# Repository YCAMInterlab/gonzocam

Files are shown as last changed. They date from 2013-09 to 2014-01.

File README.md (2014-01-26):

# gonzocam


Open source hardware kit for disposable camera or iPhone to take pictures of wild animals automatically.

gonzocam（ゴンゾカム）は市販のインスタントカメラを使って人間含む野生動物を自動撮影するためのオープンソースハードウェアキットです。インスタントカメラに装着することで、周囲の物体の動きや加速度の変化などをトリガーにシャッターを切り、自動的にフィルムを巻き上げるなどカメラ本来の機能を拡張することができます。

詳しい情報は[YCAM Interlab | gonzocam](http://interlab.ycam.jp/projects/gonzocam)を参照してください。

## Licenses

### Hardware of gonzocam

<a rel="license" href="http://creativecommons.org/licenses/by-sa/3.0/deed.en_US">
</a>
<br />
<span xmlns:dct="http://purl.org/dc/terms/" property="dct:title">Circuit diagram, Parts list, Gerber format data</span> by <a xmlns:cc="http://creativecommons.org/ns#" href="http://yang02.org/" property="cc:attributionName" rel="cc:attributionURL">yang02</a> is licensed under a <a rel="license" href="http://creativecommons.org/licenses/by-sa/3.0/deed.en_US">Creative Commons Attribution-ShareAlike 3.0 Unported License</a>.

### Software of gonzocam

Arduino sketch by Takahiro Yamaguchi is licensed under the [Apache License, Version2.0](http://www.apache.org/licenses/LICENSE-2.0.html)

    Copyright 2013 Takahiro Yamaguchi

    Licensed under the Apache License, Version 2.0 (the "License");
    you may not use this file except in compliance with the License.
    You may obtain a copy of the License at

       http://www.apache.org/licenses/LICENSE-2.0

    Unless required by applicable law or agreed to in writing, software
    distributed under the License is distributed on an "AS IS" BASIS,
    WITHOUT WARRANTIES OR CONDITIONS OF ANY KIND, either express or implied.
    See the License for the specific language governing permissions and
    limitations under the License.

### Hardware of igonzocam

<a rel="license" href="http://creativecommons.org/licenses/by-sa/3.0/deed.en_US">
</a>
<br />
<span xmlns:dct="http://purl.org/dc/terms/" property="dct:title">Circuit diagram, Parts list</span> by <a xmlns:cc="http://creativecommons.org/ns#" href="http://www.inafact.net/" property="cc:attributionName" rel="cc:attributionURL">inafact</a> is licensed under a <a rel="license" href="http://creativecommons.org/licenses/by-sa/3.0/deed.en_US">Creative Commons Attribution-ShareAlike 3.0 Unported License</a>.

### Software of igonzocam

iOS software by YCAM InterLab and Takanobu Inafuku are licensed under the [Apache License, Version2.0](http://www.apache.org/licenses/LICENSE-2.0.html)

    Copyright 2013 YCAM InterLab and Takanobu Inafuku

    Licensed under the Apache License, Version 2.0 (the "License");
    you may not use this file except in compliance with the License.
    You may obtain a copy of the License at

       http://www.apache.org/licenses/LICENSE-2.0

    Unless required by applicable law or agreed to in writing, software
    distributed under the License is distributed on an "AS IS" BASIS,
    WITHOUT WARRANTIES OR CONDITIONS OF ANY KIND, either express or implied.
    See the License for the specific language governing permissions and
    limitations under the License.

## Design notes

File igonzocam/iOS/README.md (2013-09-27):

# GonzoCam for iOS

## Description

Application for iOS to take pictures of wild animals automatically.

## Requirements & Tested

* Apple Mac OSX 10.8.4+
* Xcode 4.6 + iOS6 SDK (now developing with Xcode 5 + iOS7 SDK)
* [Cinder](http://libcinder.org)
   use latest version from github http://github.com/cinder/Cinder OR [packaged version 0.8.5](http://libcinder.org/download/)
* Tested devices: iPhone 5, iPod Touch(5th Gen)

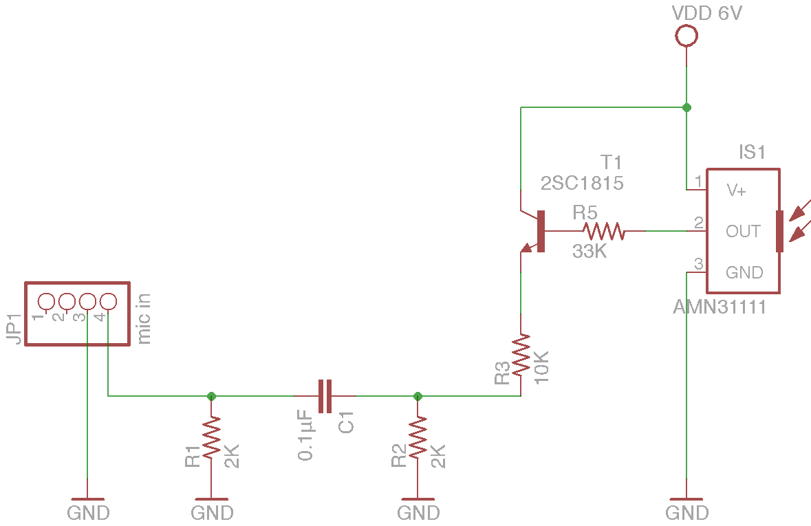
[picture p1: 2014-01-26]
igonzocam/hardware/igonzocam_motionsensor_schematic.png

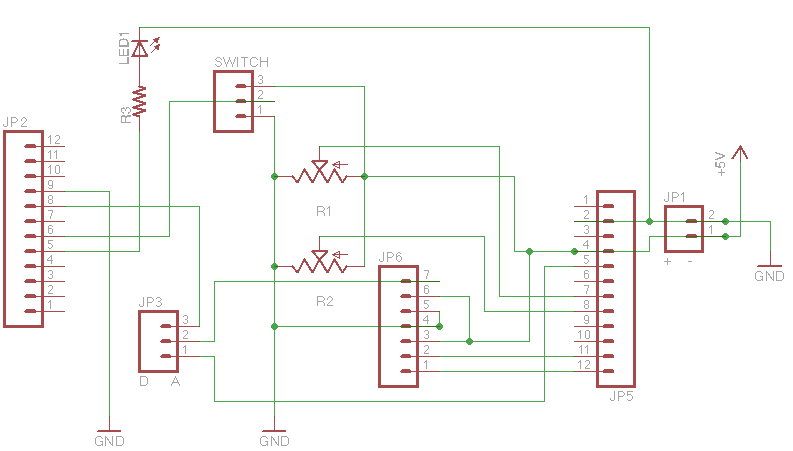
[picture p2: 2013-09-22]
gonzocam/arduino_pro_mini_shield/schematic.png

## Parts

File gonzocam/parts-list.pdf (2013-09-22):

品目 | 単価（円） | 購入先 | URL | 備考
制御基板関係パーツ
Arduino pro mini | 1,094 | スイッチサイエンス | http://www.switch-science.com/catalog/946/
半固定ボリューム | 200 | 秋月 | http://akizukidenshi.com/catalog/g/gP-02470/ | 1パック10個入り
小型スライドスイッチ | 100 | 秋月 | http://akizukidenshi.com/catalog/g/gP-02736/ | 1パック4個入り
カーボン抵抗 1/6W 330Ω | 100 | 秋月 | http://akizukidenshi.com/catalog/g/gR-16331/ | 1パック100本入り
青色LED 3mm | 100 | 秋月 | http://akizukidenshi.com/catalog/g/gI-03988/ | 1パック10個入り
ピンソケット 低メス | 60 | 秋月 | http://akizukidenshi.com/catalog/g/gC-03138/ | 1本20P、Arduino1個につき24P
ピンヘッダ 低オス | 40 | 秋月 | http://akizukidenshi.com/catalog/g/gC-02900/ | 1本40P、1基板につき24P
L字ピンヘッダ | 84 | 千石 | http://www.sengoku.co.jp/mod/sgk_cart/detail.php?code=65KM-8MJG | 1本40P、1基板につき9P
L字ピンヘッダ | 50 | 秋月 | http://akizukidenshi.com/catalog/g/gC-01627/ | 1本40P、上のやつと折れ方が違う
ジャンパーピン | 100 | 秋月 | http://akizukidenshi.com/catalog/g/gP-03687/ | 25個入り
ピンヘッダ オス | 40 | 秋月 | http://akizukidenshi.com/catalog/g/gC-00167/ | 1本40P、1基板につき3P

センサー基板関係パーツ
NaPiOn スポット検出タイプ | 1,103 | 千石 | http://www.sengoku.co.jp/mod/sgk_cart/detail.php?code=5A2C-NNGD
ユニバーサル基板 | 120 | 秋月 | http://akizukidenshi.com/catalog/g/gP-03230/ | Arduino pro miniシールドプリント基板が ない場合は、そこ用にも使用
カーボン抵抗 1/6W 1MΩ | 100 | 秋月 | http://akizukidenshi.com/catalog/g/gR-16105/ | 1パック100本入り
積層セラミックコンデンサ 0.1μF | 100 | 秋月 | http://akizukidenshi.com/catalog/g/gP-06165/ | 25本入り
ロングピンソケット | 70 | 秋月 | http://akizukidenshi.com/catalog/g/gC-05779/ | カメラ1個につき9P
熱収縮チューブ | 50 | 秋月 | http://akizukidenshi.com/catalog/g/gP-06788/

その他の電子パーツ
サーボモータTurnigy TG9e 9g x2 個 | 200 | Hobby King | http://goo.gl/oYUSO | Hobby Kingが一番安いけど届くの超絶遅 いので国内のネット通販で扱ってる店探 すのが吉
電池ボックス 単4x4本 | 150 | 秋月 | http://akizukidenshi.com/catalog/g/gP-00735/
単4電池 | 100 | 100円ショップ | | 1パック4本入り

カメラ＋筐体素材
写ルンです | | コンビニ
アクリル板 3mm | | ホームセンター | 筐体とサーボカバー、一部サーボパーツ 用
アクリル板 5mm | | ホームセンター | サーボヘッド用
さら小ねじ 3Mx20mm | 100 | ホームセンター | 1パック8本入り

その他拡張パーツ等
音声センサーモジュール | 600 | aitendo | http://www.aitendo.com/product/3186
傾きセンサーモジュール | 750 | aitendo | http://www.aitendo.com/product/3201
iPhone用広角レンズ | | Amazon | | 広角で撮りたい時。iPhone用のレンズが ぴったりはまります
アガスチ材 | | ホームセンター | | 筐体を木で作りたい時
防水ケース | 100 | Seria（100円ショップ） | http://cache.gyazo.com/44991e6d72c8e802ef84692265c6ad19.png | Seriaにちょうどいいのが売ってます
- 単価、購入先、URLはあくまで参考です、同様の型でより安いものや、代替できるパーツでも問題ありません。
- Arduino pro miniシールドのプリント基板が手元にない場合は gonzocam> arduinoProMini_shield> schematic.png を参考にユニバーサル基板で回路を作成してください。
- ”その他拡張パーツ等”は必ず必要なパーツではありません、適宜必要に応じて揃えてください。

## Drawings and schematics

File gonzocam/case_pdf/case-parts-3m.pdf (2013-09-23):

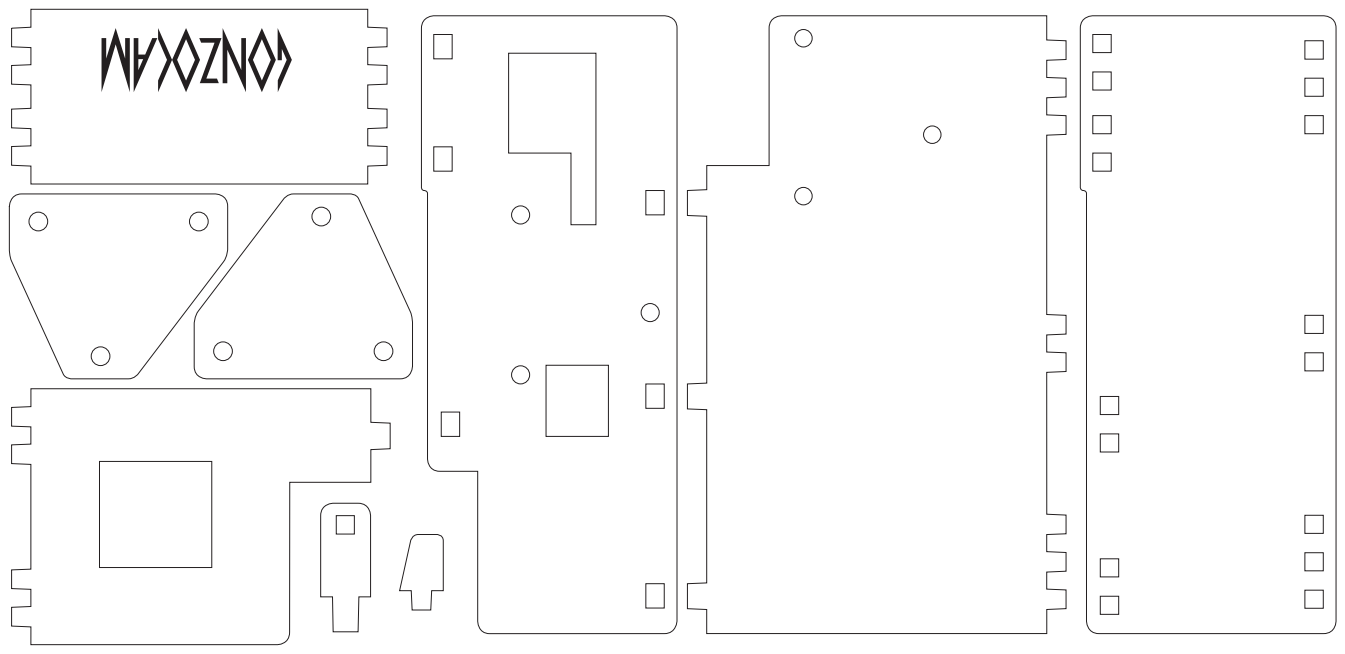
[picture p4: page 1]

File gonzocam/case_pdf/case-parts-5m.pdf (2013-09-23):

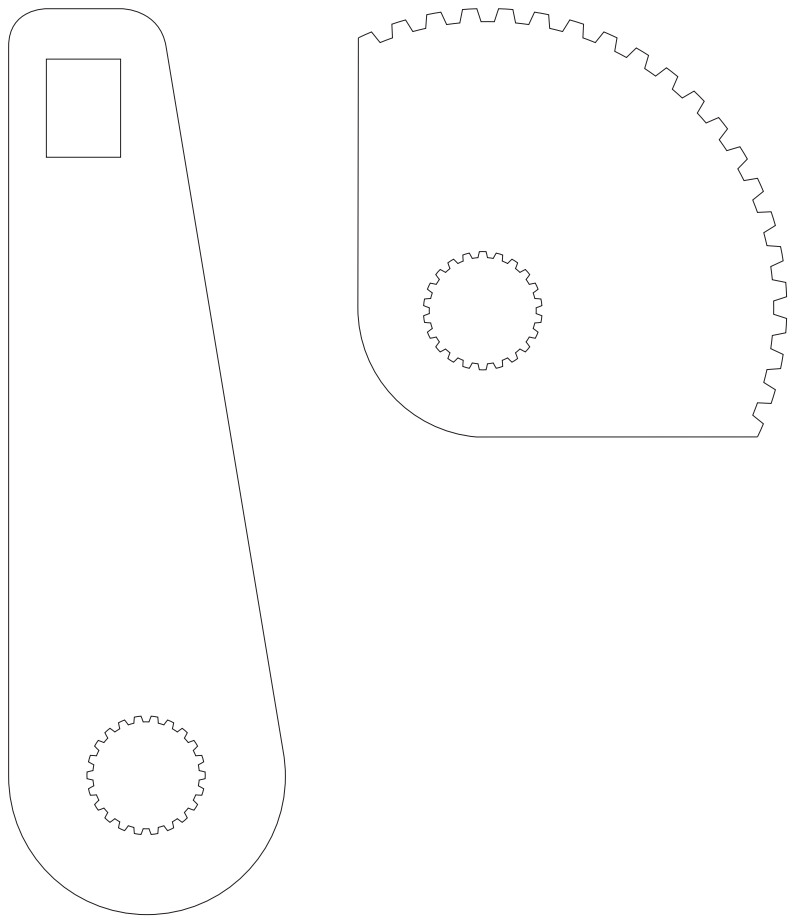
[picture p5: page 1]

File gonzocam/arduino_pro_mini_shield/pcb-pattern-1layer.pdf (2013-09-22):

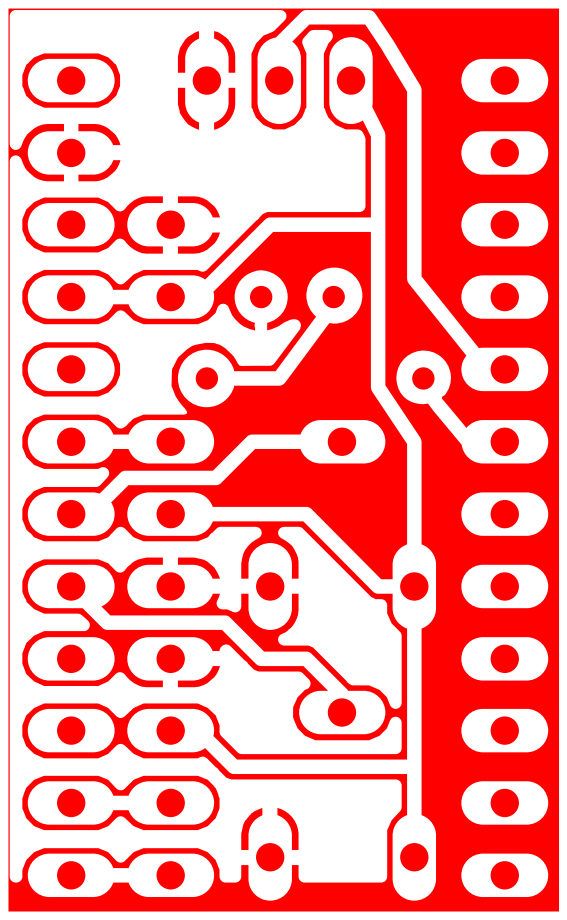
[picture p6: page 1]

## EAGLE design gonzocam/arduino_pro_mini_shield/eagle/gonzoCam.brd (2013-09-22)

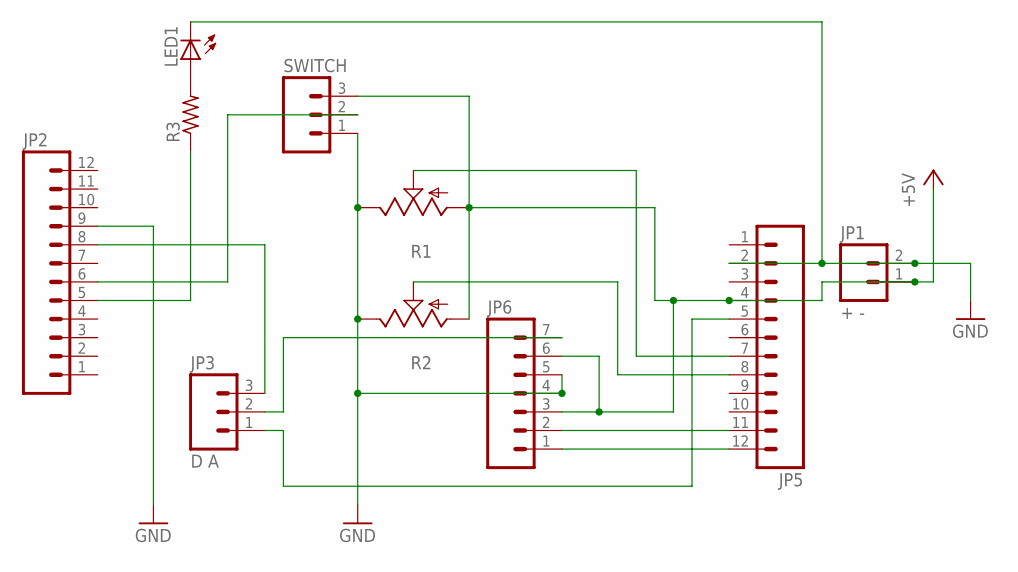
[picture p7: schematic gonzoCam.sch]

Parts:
JP1: + -; 1X02
JP2, JP5: M12PTH; 1X12
JP3: D A; 1X03
JP6: M07; 1X07
LED1: LED3MM
R1, R2: TRIM_US-CA6V; CA6V
R3: R-US_0204/5; 0204/5
SWITCH: M03PTH; 1X03

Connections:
+5V: JP1.1, JP5.4, JP6.3, JP6.6, R1.A, R2.A, SWITCH.3
GND: JP1.2, JP2.9, JP5.2, JP6.4, JP6.5, LED1.K (C), R1.E, R2.E, SWITCH.1
unnamed: JP2.6, SWITCH.2
unnamed: JP2.5, R3.1
unnamed: JP5.11, JP6.2
unnamed: JP5.12, JP6.1
unnamed: JP3.2, JP6.7
unnamed: JP5.8, R2.S
unnamed: JP5.7, R1.S
unnamed: LED1.A, R3.2
unnamed: JP2.8, JP3.3
unnamed: JP3.1, JP5.5

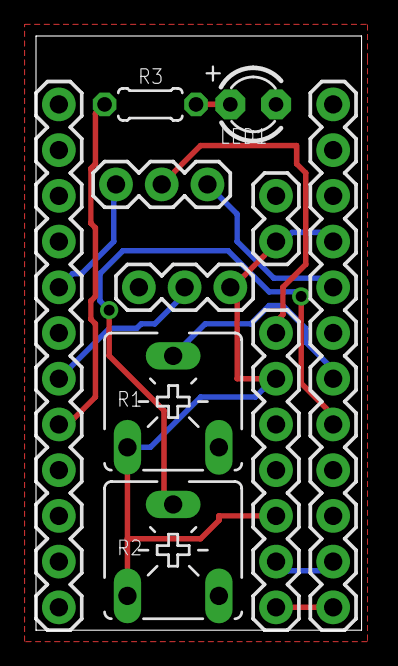
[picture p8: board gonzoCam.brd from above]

Board: 2 copper layers, 18.1 x 33.0 mm, 10 parts (0 on the bottom side), 12 nets.

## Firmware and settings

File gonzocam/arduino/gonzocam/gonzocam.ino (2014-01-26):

/*
 * Copyright 2013 Takahiro Yamaguchi
 *
 * Licensed under the Apache License, Version 2.0 (the "License");
 * you may not use this file except in compliance with the License.
 * You may obtain a copy of the License at
 *
 *   http://www.apache.org/licenses/LICENSE-2.0
 *
 * Unless required by applicable law or agreed to in writing, software
 * distributed under the License is distributed on an "AS IS" BASIS,
 * WITHOUT WARRANTIES OR CONDITIONS OF ANY KIND, either express or implied.
 * See the License for the specific language governing permissions and
 * limitations under the License.
 */

#include <avr/sleep.h>
#include <Servo.h>

// pin assign -------------//
#define POT0    A0
#define POT1    A1
#define SENSOR  A3 //if use digital input > set 2
#define SWITCH  4
#define LED     5
#define SV_PUSH 10
#define SV_ROLL 11

//parameters
const long initialDelay    = 20000;
const int pushDuration     = 200;
const int rollCount        = 4;
const int shootDelayMin    = 0;
const int shootDelayMax    = 3000;
const long waitingTimeMin  = 10000;
const long waitingTimeMax  = 120000;
const int pushOff          = 50;
const int pushOn           = 75;
const int blinkInterval    = 500;

//define servo
Servo servoRoll;
Servo servoPush;

//for sequence
boolean shootMode = false;
boolean waitMode = false;
long timeStampShoot = 0;
long timeStampWait = 0;
unsigned int shootDelay;
unsigned long waitingTime;

//sensor
byte sensorLevel;
byte sensorLevelDef;
unsigned int countSensing;
unsigned int countSensingThreshold;

//calibration
unsigned int countLevelLow = 0;
unsigned int countLevelHigh = 0;
unsigned long sensorValLow;
unsigned long sensorValHigh;



void setup()
{
  Serial.begin(9600);

  //Define pin mode
  pinMode(SENSOR, INPUT);
  pinMode(LED, OUTPUT);
  pinMode(SV_ROLL, OUTPUT);
  pinMode(SV_PUSH, OUTPUT);

  //Initialize servo
  servoRoll.attach(SV_ROLL);
  servoPush.attach(SV_PUSH);
  servoRoll.write(180);
  servoPush.write(pushOff);

  //Chnage the sensor mode by switch
  String sensorName;
  if(digitalRead(SWITCH)) sensorName = "MOTION";
  else sensorName = "MIC";
  calibration(sensorName);
  countSensing = 0;

  //save the battery
  set_sleep_mode(SLEEP_MODE_IDLE);
  sleep_mode();
}

void loop(){
  int val = analogRead(SENSOR);
  if(val < 1023/2) sensorLevel = 0;
  else if(val > 1023/2) sensorLevel = 1;

  if(sensorLevel == sensorLevelDef) countSensing = 0;
  else{
    countSensing++;
    Serial.println(countSensing);
  }

  //WAIT MODE //////////////////////////////////////////////////////////////
  if(!shootMode && !waitMode && countSensingThreshold < countSensing){
    Serial.println("SENCING!");
    digitalWrite(LED, HIGH);
    timeStampShoot = millis();
    shootMode = true;
  }

  //SHOOT MODE //////////////////////////////////////////////////////////////
  if(shootMode && !waitMode && timeStampShoot + shootDelay < millis()){

    while(millis() < timeStampShoot + shootDelay + pushDuration){
      servoPush.write(pushOn);
    }
    digitalWrite(LED, LOW);
    servoPush.write(pushOff);
    Serial.println("SHOOT!");

    for(int i=0; i<rollCount; i++){
      for(int j=180; j>0; j--){
        servoRoll.write(j);
        delay(3);
      }
      delay(300);
      servoRoll.write(180);
      delay(500);
    }

    timeStampWait = millis();
    waitMode = true;
    shootMode = false;
  }

  //INTREVAL MODE //////////////////////////////////////////////////////////////
  if(!shootMode && waitMode){
    if(millis() < timeStampWait + waitingTime){
      int i = int((millis() - timeStampWait) / blinkInterval);
      if(i % 2 == 0) digitalWrite(LED, LOW);
      else if(i % 2 == 1) digitalWrite(LED, HIGH);
    }
    else if(timeStampWait + waitingTime < millis()){
      waitMode = false;
      digitalWrite(LED, LOW);
      countSensing = 0;

      set_sleep_mode(SLEEP_MODE_IDLE);
      sleep_mode();
    }
  }

}


void calibration(String sensor){

  while(millis() < initialDelay){
    digitalWrite(LED, HIGH);

    int val = analogRead(SENSOR);
    if(val < 1023/2){
      countLevelLow++;
      sensorValLow = sensorValLow + val;
    }
    else if(val > 1023/2){
      countLevelHigh++;
      sensorValHigh = sensorValHigh + val;
    }
  }

  //define sensor condition
  int valLow = sensorValLow / countLevelLow;
  int valHigh = sensorValHigh / countLevelHigh;

  //set the default sensor state
  if(countLevelLow > countLevelHigh) sensorLevelDef = 0;
  else if(countLevelLow < countLevelHigh) sensorLevelDef = 1;

  //set wating duration by sensor value
  shootDelay = map(analogRead(POT0), 1023, 0, shootDelayMin, shootDelayMax);
  waitingTime = map(analogRead(POT1), 1023, 0, waitingTimeMin, waitingTimeMax);

  //set the threshold by the kind of sensor
  if(sensor == "MIC") countSensingThreshold = 10;
  else if(sensor == "MOTION") countSensingThreshold = 30;

  //sign of finished calibration
  while(millis() < initialDelay + 600){
    int i = int((millis() - initialDelay) / 100);
    if(i % 2 == 0) digitalWrite(LED, LOW);
    else if(i % 2 == 1) digitalWrite(LED, HIGH);
  }

  //for debug
  Serial.print("Count Low = ");
  Serial.print(countLevelLow);
  Serial.print("  ");
  Serial.print("Val Low = ");
  Serial.println(valLow);

  Serial.print("Count High = ");
  Serial.print(countLevelHigh);
  Serial.print("  ");
  Serial.print("Val High = ");
  Serial.println(valHigh);

  Serial.print("Level Def = ");
  Serial.println(sensorLevelDef);
  Serial.println();

  Serial.print("Shoot Delay = ");
  Serial.println(shootDelay);
  Serial.print("Wating Time = ");
  Serial.println(waitingTime);

  digitalWrite(LED, LOW);

}

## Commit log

2013-09-12 Update README.md
    ダミー文章、ダミー画像、ライセンス文章の追加
2013-09-22 Uploaded .ino code for Arduino
2013-09-22 Uploaded circuits data
    [gonzoCam.brd, gonzoCam.sch]
2013-09-23 Uploaded pdf files for camera case
2013-09-23 Fixed pdf data
    gonzocamロゴ入ってなかったので上げなおし
2014-01-26 add igonzocam hardware
    [igonzocam_motionsensor.sch]

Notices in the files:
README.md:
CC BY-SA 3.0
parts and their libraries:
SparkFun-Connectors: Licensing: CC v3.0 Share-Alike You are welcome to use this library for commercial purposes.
